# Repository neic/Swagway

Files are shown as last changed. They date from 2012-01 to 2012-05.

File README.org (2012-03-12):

* Swagway
The Swagway is a Segway clone.

It is a school project at HTX Frederikshavn.

** Mechanical
It consists of a welded steel frame with two motors and gearbox assemblies from a powered wheelchair. The motors are 140W each and run on 24V. The batteries are two cheap 12V 18Ah lead batteries.

** Electronics
The electronics is build around an Arduino. It gets it input from a ADXL345 accelerometer and a ITG-3200 gyro and drives the motors through two HEXFET bridges.

The schematic and board layouts are in Electronics/

** Software
The software for the Arduino onboard the Swagway is located in Software/swagway/

A Processing application with a rolling graph for debugging the angles is located in Software/graph/

** Rapport
A rapport (in danish) on the complete build process will be located in Rapport/

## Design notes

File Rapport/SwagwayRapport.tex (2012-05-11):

\documentclass[a4paper,final,11pt,oneside,article,danish,table]{memoir}
\checkandfixthelayout
\XeTeXtracingfonts= 1
\usepackage{babel,microtype,verbatim,threeparttable,amsmath,amssymb,unicode-math,hyperref,siunitx,mhchem,tikz,pgfplots,tikz-timing,pdfpages}
\sisetup{per-mode=symbol}
\microtypesetup{final,verbose=silent}
\usetikzlibrary{mindmap,arrows,positioning,shapes}
%\setmainfont[Ligatures={TeX}]{Arno Pro}
\setmainfont{Linux Libertine O}
\setmathfont{[Asana-Math]}
%\hfuzz=1pt
\usepackage[margin]{fixme}
\fxusetheme{color}

\newcommand{\authorvar}{Carl-Emil~Grøn~Christensen \& Mathias~Dannesbo}
\newcommand{\pretitlevar}{Teknikfag~A~eksamen:}
\newcommand{\titlevar}{Swagway} 
\newcommand{\subtitlevar}{0} 
\newcommand{\datevar}{\today} 
\newcommand{\subjectvar}{Teknikfag~A:~El}
\newcommand{\classvar}{EUC~Nord: HTX~Frederikshavn, f11htx3.B}
\newcommand{\teachervar}{Allan~Gilarska}

\makepagestyle{articlehead}
\makeevenhead{articlehead}{}{\classvar\\\titlevar}{\datevar}
\makeevenfoot{articlehead}{}{\thepage}{}
\makeoddhead{articlehead}{}{\classvar\\\titlevar}{\datevar}
\makeoddfoot{articlehead}{}{\thepage}{}
\pagestyle{articlehead}

\usepackage{listings,textcomp}
\lstset{language=[Visual]C++,
  morekeywords={[2]abs,acos,asin,atan,atan2,ceil,constrain,cos,degrees,exp,floor,log,map,max,min,radians,random,randomSeed,round,sin,sq,sqrt,tan,bitRead,bitWrite,bitSet,bitClear,bit,highByte,lowByte,analogReference,analogRead,analogWrite,attachInterrupt,detachInterrupt,delay,delayMicroseconds,digitalWrite,digitalRead,interrupts,millis,micros,noInterrupts,noTone,pinMode,pulseIn,shiftIn,shiftOut,tone,Serial,Serial1,Serial2,Serial3,begin,end,peek,read,print,println,available,flush,setTimeout,find,findUntil,parseInt,parseFloat,readBytes,readBytesUntil},
  keywordstyle={\bfseries\color[rgb]{0,0,1}},
  keywordstyle={[2]\bfseries\color[rgb]{0.8,0.33,0}},
  identifierstyle=\ttfamily,
  commentstyle=\color[rgb]{0.133,0.545,0.133},
  stringstyle=\color[rgb]{0.627,0.126,0.941},
  showstringspaces=false,
  basicstyle=\small\ttfamily,
  numberstyle=\footnotesize,
  numbers=left,
  stepnumber=1,
  numbersep=10pt,
  tabsize=2,
  breaklines=true,
  breakatwhitespace=false,
  upquote=true,
  extendedchars=true,
  literate={æ}{{\ae}}1
    {ø}{{\o}}1
    {å}{{\aa}}1
}

\tikzstyle{block} = [draw, fill=blue!20, rectangle, 
    minimum height=1.5em, minimum width=5em]
\tikzstyle{sum} = [draw, fill=blue!20, circle, node distance=1cm]
\tikzstyle{input} = [coordinate]
\tikzstyle{output} = [coordinate]

\newcommand{\swino}[2]{\lstinputlisting[firstnumber=#1,firstline=#1,lastline=#2]{../Software/swagway/swagway.ino}}
\newcommand{\adxlh}[2]{\lstinputlisting[firstnumber=#1,firstline=#1,lastline=#2]{../Software/swagway/ADXL345.h}}
\newcommand{\adxlc}[2]{\lstinputlisting[firstnumber=#1,firstline=#1,lastline=#2]{../Software/swagway/ADXL345.cpp}}
\newcommand{\itgh}[2]{\lstinputlisting[firstnumber=#1,firstline=#1,lastline=#2]{../Software/swagway/ITG3200.h}}
\newcommand{\itgc}[2]{\lstinputlisting[firstnumber=#1,firstline=#1,lastline=#2]{../Software/swagway/ITG3200.cpp}}
\newcommand{\boarddate}[1]{\marginpar{\tiny\textcolor{blue!80!black}{#1}}}
\newcommand{\issue}[1]{\textsuperscript{\textcolor{blue!80!black}{\href{https://github.com/neic/Swagway/issues/#1}{\##1}}}}

\begin{document}
% \includepdf{forside.pdf} \clearpage%------------------------ Forside

\noindent
{\fontsize{90}{108}\selectfont \color{red!80!black}\titlevar}\\
\vfill
\noindent
{\color{blue!90!black} \LARGE
{\fontsize{16.55}{20}\selectfont \authorvar}\\
\begin{tabular*}{\textwidth}{@{\extracolsep{\fill}} ll}
  \subjectvar & \datevar\\
\end{tabular*}
}

\thispagestyle{empty}
\clearpage
\includepdf{TroogLove.pdf}
\includepdf{TroogLove.pdf}
\begin{center}
  \if\pretitlevar 0
  \else{\Large\pretitlevar\\} \fi
  \textsc{\HUGE\titlevar\\}
  \if\subtitlevar 0
  \else {\Large\subtitlevar\\} \fi
  %\vspace{1em}
  {\LARGE 
  af\\
   \authorvar}\\
\end{center}

\vfill

\noindent
\begin{tabular*}{\textwidth}{@{\extracolsep{\fill}} ll}
  \classvar&\subjectvar\\
  {Lærer: }\teachervar & \datevar\\
\end{tabular*}
\thispagestyle{empty}
\clearpage

\chapter*{Forord}\label{chap:for}
Gennem teksten vil der være angivet link til “Issues” på GitHub siden for projektet.\footnote{\url{https://github.com/neic/Swagway}} Disse Issues har været brugt som projektstyring samt bugtracker igennem projektforløbet. Links er angivet som i enden af denne sætning.\issue{1} Det er ikke nødvendigt for forståelsen af denne rapport at følge linksne.

Vi vil gerne takke Steffen Linnerup Christiansen for hjælp med mekanikken, samt Kristian Holm Nielsen for hjælp med forståelsen af PID.

\clearpage \setcounter{tocdepth}{1} \tableofcontents \clearpage

\chapter{Indledning}\label{chap:ind}
Transport enheder bliver mere og mere avancerede, og der skabes ofte nye enheder. Specielt mobilitet og anvendelighed har været i højsædet i mange nye produkter. Det handler om hurtigt at kunne komme fra punkt a til punkt b, uden at det kræver større besvær. Derudover er løsninger som er intuitive at bruge også fremskreden, og et produkt som opfylder alle disse punkter er Segwayen. Den er hurtig, kræver næsten ingen erfaring at køre på og er lille. Man kan hurtigt suse fra en afdeling til anden. 

Formålet med projektet er at bygge en motoriseret selvbalancrende tohjulet transportenhed. Det er en klon af en Segway som er et kommercielt produkt. Kendetegnet ved Segwayen er, at de to hjul sidder på samme aksel, hvor elektronik og motorene sørger for at, selv med en fører, holde enheden i balance.
\begin{figure}[htbp]
  \centering
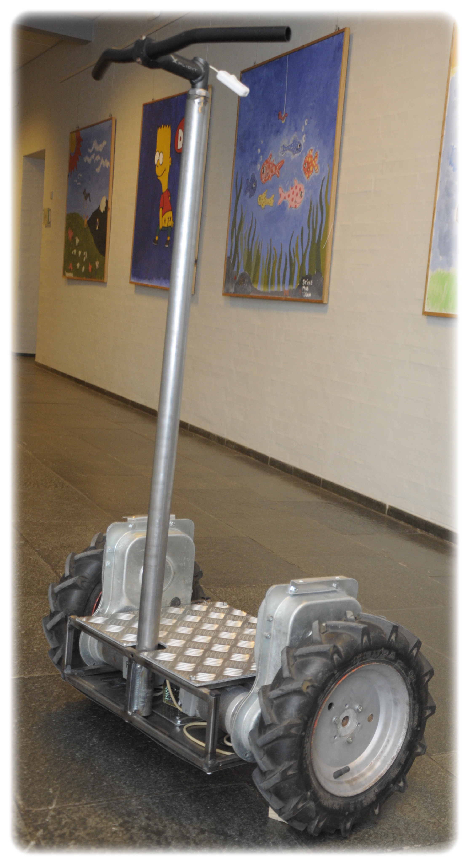
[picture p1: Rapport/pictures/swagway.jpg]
  
  \caption{Den mekaniske udformning af Swagway}
  % \label{fig:}
\end{figure}
Når en fører læner sig frem eller tilbage, kompenserer Segwayen ved køre i samme retning, for atter at balancere den. For at dreje enheden vipper føreren håntaget til den ene eller anden side, som man ønsker at dreje til. Segwayen kan købes for cirka halvfjerdstusinde kroner, hvis man ønsker at eje sådan en.

Projektoplæget lyder:
\begin{quote}
  Formålet er at bygge en balance robot på to hjul,v z en Segway klon. Minimums målet er at få robotten til at balancere. Derefter få den til at køre og kunne styre den hvis tid og evner rækker til det.
\end{quote}

Hovedeudfordringen er at holde enheden lodret. For at gøre dette skal man kende enhedens vinkel i forhold til lodret og omsætte denne vinkel til et signal til motorene. Når vinklen stiger driver motorene hjulene som så flytter enheden og brugerens tygdepunk ind over akslen igen.
Det kan se som tre isolerede problemstillinger som passer ind i I-C-O-modellen:
\begin{itemize}
\item[Input] Måle Swagwayens hældning i forhold til lodret
\item[Control] Omsætte vinklen til et signal til motorene.
\item[Output] Drive to motore baseret på signalet.
\end{itemize}

Projektet er udarbejdet ud fra mikrokontrolleren Arduino Uno, i programmet arduino. Mikrokontrolleren bliver programmeret via. programmet Arduino, som nærmest er i sproget C++ med et Arduino bibliotek. Da vi har modtaget undervisning i denne platform, har dette været det oplagte redskab at benytte til løsningen.

\chapter{Input}
\section{Sensor}
Efter nogen research af andre køretøjer og mindre robotter der fungerer på sammen måde, var det klart at gyroskoper og accelerometere kunne måle vinklen så hurtigt og præcist som det var krævet.
\subsection{Sensor hardware}
Gyroskoper og accelerometere har indtaget forbrugerens produkter, og kortlægger allerede nu deres bevægelser. De faldende priser og faldene energiforbrug har gjort, at gyroskoper og accelerometere er langt mere tilgængelige for alle. Mobiltelefoner, spilkonsoller og kameraer kan nu måle hvordan du bevæger dig, og flere og flere enheder importerer også disse bevægelses sensorer, for at adskille sig fra de andre.

Disse bevægelses sensorer er avancerede MEMS (mikroelektromekaniske systemer) teknologier, som inkoorpererer gyroskoper, accelerometere og kompas sensorer. % Bevægelses behandling foretages oftest med en kombination af to sensorer, for at få optimal præcision.
I dette projekt har vi arbejdet med gyroskoper og accelerometere, som vi også kender fra vores smartphones. Swagwayen skal, lige som en smartphone kan måle om den står eller ligger ned, måle i hvilken vinkel den står i.   

\subsubsection{Gyroskop}
Et gyroskop måler vinkelhastigheder, hvor hurtigt noget drejer om en akse. Hvis denne vinkelhastighed integreres over tid finder man vinklen som gyroskopet har flyttet sig. Problemet med at integrere gyroskopdata er, at pga. måleusikkerheder vil det målte nulpunkt drive væk fra det fysiske nulpunkt. Moderne gyroskoper er en MEMS. Det betyder, at det både er en mekanisk og elektrisk funktion i et system.

\subsubsection{Accelerometer}
Et accelerometer kan måle accelerationer. Man kan med hjælp fra tangens og data fra to akser udregne den vinklen accelerometeret står i forhold til jordens tyngdekraft. Problemet med dette er at accelerometer måler alle accelerationer, ikke kun jordens tyngdekræft. Når Swagwayen fx accelerer, bremser eller køre over en sten bliver den udregnede vinkel forkert, da denne også frembringer en spike i accelerationsmålingen.
\begin{figure}[htbp]
  \centering
  
  \caption{Et accelerometers interne MEMS-struktur}
  \label{fig:memsacc}
\end{figure}
Et accelerometer måler en bevægelse, som enten er forårsaget af tyngdekraften eller en bevægelse. Som set på figur \ref{fig:memsacc} måles accelerationen i et moderne MEMS accelerometer ved en ændring i kapacitansen, $c$, som skyldes en ændring i massen, $m$, position. Kapasitansen fører til en ændring i spændingen, som herefter digitaliseres via ADC og kan benyttes af en mikrokontroller som Arduinoen. Dette gøres for de tre akser x, y og z, og accelerationen kan nu måles i alle retninger.

\subsubsection{IMU}
For at løse problemet med at gyroskopet driver og problemet med at accelerometret ikke er nøjagtig når det bliver påvirket af andre accelerationer end tygdekraften kan man bruge begge sensorer sammen. Man bruger begge sensoreres data og samler dem i et filter. Se mere herom i sektion \ref{sec:filter}.

De fleste moderne accelerometere og gyroskoper kommer i små SMD pakker som er vanskelig håndlodde. Heldigvis er det forholdsvis let at få disse sensorer monteret på et breakoutboard. Efter at have kigget på andre Segway kloner og balancerobotter faldt valget på en IMU fra Sparkfun. Se figur \ref{fig:imu}. En inertial measurement unit, IMU, er en enhed som kombinerer flere sensorer.
\begin{figure}[htbp]
  \centering
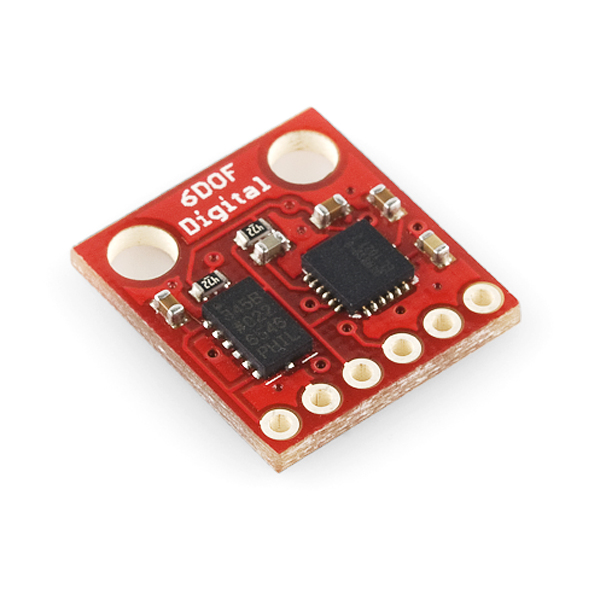
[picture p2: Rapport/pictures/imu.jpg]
  
  \caption[6DOF IMU breakoutboard fra Sparkfun]{6DOF IMU breakoutboard fra Sparkfun. (CC BY-NC-SA 3.0, Sparkfun)}
  \label{fig:imu}
\end{figure}
IMUen fra Sparkfun et ADXL345 accelerometer og et ITG-3200 gyroskop. Accelerometret og gyroskopet er begge tre-akset. Det giver IMUen seks frihedsgrader (DOF). Swagwayen skal dog kun bruge tre frihedsgrader; to akser fra accelerometret og en fra gyroskopet, men IMUen med seks frihedsgrader var det mindste med digital interface.

\subsection{I²C}
Kommunikation med IMUen sker digital over en I²C-bus. På bussen er der en master\footnote{Det er mulig at lave et multi-master opstilling hvis alle masterne understøtter det.} og en eller flere slaves. I Swagwayen er Arduinoen master og accelerometeret og gyroskopet er begge slaves. I²C bussen består af to fysiske forbindelser, en serial data linje (SDA) og en serial clock linje (SCL). Alle enheder på bussen forbinder til disse to forbindelser. Linjerne er open-drain med eksterne pull-op modstande. Det vil sige at i hver enhed sidder der MOSFETer der trækker spændingen på linjen mod GND efter behov. De eksterne pull-op modstande trækker linjerne op igen. Se figur \ref{fig:i2cbasic}.
\begin{figure}[htbp]
  \centering
  
  \caption{Eksempel på I²C-netværk}
  \label{fig:i2cbasic}
\end{figure}

På Arduinoen er I²C SDA på A4 og SCL på pin A5 med indbygget pull-up modstande på \SI{20}{k\ohm}--\SI{50}{k\ohm}. \cite[s. 317]{atmega} De er aktiveret som standard når man bruger Wire biblioteket.\footnote{For reference se linje 75 i \texttt{utility/twi.c} i Wire biblioteket.}

Arduinoens spænding er \SI{5}{V} og IMUens er \SI{3,3}{V}. IMUen bliver forsynet med \SI{3,3}{V} fra Arduinoen, men SDA og SCL er koblet direkte til Arduinoens pins som har \SI{5}{V} som reference. Den korrekte løsning ville være at lave en level-shifter imellem en \SI{5}{V}- og en \SI{3,3}{V}-del af I²C-bussen, men når pull-up modstandene er så høje som de er det stadig forsvarligt at kører IMUen direkte med \SI{5}{V} som $V_{IO}$-reference. Der er flere eksempler på det samme blandt andre på Internettet der bruger samme chips.

Den letteste måde at kommunikere over I²C fra en Arduino er at bruge Wire-bibliotektet som kommer sammen Arduino-softwaren: \lstinline{#include <Wire.h>} For at få Arduinoen til at tilslutte sig bussen som master kaldes \lstinline{Wire.begin();} uden parametre. Slaverne på I²C-bussen har alle en adresse som fremgår af deres respektive datablade.

ADXL345 og ITG-3200 indeholder begge flere register med forskellige funktioner. Nogle registre indeholder opsætningen for chippen, andre indeholder det data som chippen måler. Hvis man, fra Arduinoen, vil skrive til et af registrene køre man følgene kode:
\begin{lstlisting}
  Wire.beginTransmission(deviceAddress);   // begynder en session med enheden med deviceAddress
  Wire.write(regAddress); // sender adressen på den register man vil ændre
  Wire.write(value); // sender værdien registeren skal indtage
  Wire.endTransmission(); // afslutter sessionen
\end{lstlisting}

At læse et register er lidt mere omfattende:
\begin{lstlisting}
 Wire.beginTransmission(deviceAddress); // begynder en session med enheden med deviceAddress
 Wire.write(regAddress); // sender adressen på den register man vil ændre
 Wire.endTransmission(); // afslutter sessionen
  
 Wire.beginTransmission(deviceAddress); // begynder en ny session
 Wire.requestFrom(deviceAdress, numberOfBytes); // sender anmodning på at modtage numberOfBytes
 int i = 0; 
 while (Wire.available()) { // så længe der er data tilgængeligt
   buffer[i] = Wire.read(); // modtag data og fyld det i buffer
   i++;
 }
 Wire.endTransmission(); // afslutter sessionen
\end{lstlisting}

Disse to funktioner bliver senere refereret til som hhv. \lstinline{writemem()} og \lstinline{readmem()}.

\subsection{IMU biblioteker}
I begyndelsen af projektet var alt kommunikationen med ADXL345 og ITG-3200 programmeret i \texttt{swagway.ino}. Det virkede og Arduinoen modtog data fra IMUen, men koden var svær at vedligeholde og gik tit i stykker. Der var desuden en fejl igennem lægere tid der resulterede i at den vinkel der blev udregnet fra gyroskopet, \lstinline{gyroAngle}, var ca. dobbelt så stor som den burde være.\issue{20} Efter mange ufuldendte forsøg på at rette fejlen blev alt gammel kode der var releateret til I²C slettet. Der blev istedet brugt et bibliotek passende til gyroskopet hvor alle funktioner var implementeret. Biblioteket hedder ITG-3200.

Det var ikke til at finde et ligende bibliotek til accelerometret, så med inspiration fra itg3200-bibliotekt blev der skrevet et. Biblioteket består af to filer. En headerfil, \texttt{ADXL345.h}, og selve funktionaliteten, \texttt{ADXL345.cpp}.

Headerfilen indeholder først definitioner på konstanter som enhedsadressen og registere:
\adxlh{23}{35}
Værdierne og navnene er hentet fra \cite[s. 23]{adxl345} At have definitioner på alle konstanter gør koden lettere læselig, så man ikke skal søge referencer i databladet.

Efterfølgene er der defineret en klasse med alle funktioner relateret til accelerometeret:
\adxlh{37}{49}

I \texttt{ADXL345.cpp} er funktionalitet skrevet. Som eksempel er her tre af de første funktioner er begge til opsætning af accelerometret.

\subsubsection{setMeasureMode()}

\adxlc{33}{36}
\lstinline{setMeasureMode()} skriver til power control registret, \lstinline{POWER_CTL}. Funktionaliteten af \lstinline{POWER_CTL} er beskrevet i \cite[s. 25--26]{adxl345}. \lstinline{POWER_CTL}s adresse er, som tidligere beskrevet, defineret i \texttt{ADXL345.h}. \lstinline{MEASUREMODE} er en sekvens af otte bits (en byte) somm hvis de skrives i \lstinline{POWER_CTL}, vil sætte accelerometret i måle tilstand. Sekvensen er ligledes udledt af \cite{adxl345}. Den er i dette tilfælde \texttt{0000\,1000}.

\subsubsection{getOutputRate()}

\adxlc{38}{42}
\lstinline{getOutputRate()} læser registret \lstinline{BW_RATE}, ligger dataene i en buffer og retunerer aflæsningen.

\subsubsection{setFullRes()}

\adxlc{56}{60}
\lstinline{setFullRes()} skal kun ændre \emph{en} bit i registret \lstinline{DATA_FORMAT}. For at bibeholde de andre bits læser den først det som står i registret og gemmer det i en buffer. \lstinline{1 << 3} betyder en bit shiftet tre pladser til venstre: \texttt{0000\,1000}.  \lstinline{~(1 << 3)} er Bitwise NOT værdien af dette: \texttt{1111\,0111}. Det bliver AND med bufferen, \lstinline{(_buff[0] & ~(1 << 3))}. Det er lig med alle de bit som er sat i bufferen på nær den fjerde sidste. Altså: den sætter den fjerde sidste bit til 0 og bibeholder alle andre. \lstinline{(_fullRes << 3)} er værdien der skal sætte shiftet tre pladser til venstre: \texttt{0000\,x000}. Disse to værdier bliver til slut OR med hinanden og den fjerde sidste bit er nu ændret til værdien af \lstinline{_fullRes} uden at nogle andre bits bliver ændret. Denne værdi bliver nu skrevet tilbage i samme buffer.

To andre eksempler på funktionaliteten af \texttt{ADXL345.cpp}. Disse funktioner har med modtagelse af data at gøre.

\subsubsection{isRawDataReady()}
\adxlc{75}{79}
Accelerometeret har et register med interrupt flag, \lstinline{INT_SOURCE}. \lstinline{isRawDataReady()} læser dette register og gemmer det i en buffer. Bufferen bliver shiftet syv pladser til højre og  \lstinline{isRawDataReady()} returnerer en bool værdi, alt efter, om interrupt flaget er sat.

\subsubsection{readAccRaw()}
\adxlc{99}{105}
Dataen i accelerometeret fylder seks registre af 8 bit. Hver akse fylder to registre hvoraf det første er den mindst betydene. \lstinline{readAccRav()} læser \lstinline{DATAX0} og seks registre frem. Dataen bliver lagt i et buffer-array. Den mest betydene af de to bytes som hører sammen bliver shiftet 8 pladser til venstre og derefter AND med den mindst betydene. De to bytes bliver sat sammen direkte efter hindanden. Værdierne bliver retuneret til tre integer-pointers.

\section{Styring}
Styringen af Swagwayen skulle være en længerevarende og holdbar løsning. Det ønskes ikke, at enheden efter forholdsvis kort tid skulle udskiftes eller repareres. Vi overvejede fem forskellige løsninger: En lineær potentiometer, et drejepotentiometer, gaffelsensor, strain-gate og stepper motor.
\subsection{Lineær potentiometer} 
Et lieært potentiometer fungerer som et normalt potentiometer, dog trækkes "armen" i en sliske.
Potentiometret skal placeres i bunden af stangen, hvorefter potentiometrets arm trækkes med stangens bevægelse. Herefter vil man kunne ændre på PWM signalet til motorene, og på den måde dreje. Løsningen er simpel at udføre, og vil virke let i praksis.

Ulempen ved denne løsning er dog, at potentiometret hurtigt slides op ved brug, og det er derfor ikke en holdbar løsning.
\subsection{Dreje potentiometer}
Samme princip fra det lineæere potentiometer gælder her. Derimod drejes dette potentiometer i stedet for om sin egen akse. Ideen med dette var, at man let kan implementere den i toppen af Swagwayens styr, og så styre PWM signalet til motorerene sådan. 

Lige som det linæere potentiometer, slides denne løsning hurtigt, og er derfor ikke holdbar. Derudover er denne løsning ikke lige så intuitiv og føles klodset, hvilket ikke er det vi ønsker med produktet.
\subsection{Gaffelsensor}
Gaffelsensorer benyttes i gamle kuglemuse, som vi alle nok kender. Gaffelsensorene måler hvor meget noget har flyttet sig ved at analysere bevægelsen i forhold til nogle bånd buede bånd, i to krysende retninger. Ud fra bevægelsen kan gaffelsensoren bestemme, hvordan kuglen har bevæget sig i dens socket. En lignende anordning kunne placeres i bunden af stangen lige som det lineæere potentiometer, og en kugle kunne skubbes rundt lige som i en mus, for at bestemme stangens hældningen. Løsningen er meget præcis hvis den er lavet mekanisk godt.

Gaffelsensoren er derimod ekstremt upræcis hvis mekanikken ikke er rentskåret-næsten perfekt. Yderligere bliver dens præcision påvirket af støv og skidt, hvilket hurtigt vil ophobe sig i bunden af vores Swagway.
\subsection{Strain-gate}
En strain-gate løsning er en anordning, som placeres på siden af stangen. Strain-gaten kan mærke tryk i metallet, og kan ud fra dette tryk bestemme en værdi, som man kan bruge til at styre Swagwayen med. Denne løsning er ekstrem præcis, og benyttes ofte i store maskiner.

Problemet er dog, at den ikke virker på vores stang, da den er for stiv, og løsningen hverken er intuitiv eller responsiv for forbrugeren. Den er ikke lige til at finde ud af fra første øjekast, og den er sværere at lære.
\subsection{Stepper motor}
Det sidste løsningsforslag: Stepper motor. Planen med denne var at foretage den modsatte funktion af hvad man normalt gør med en stepper motor: I stedet for at få motoren til at bevæge noget, skal styret bevæge motoren, hvorefter det måles hvilket step den er på i Arduinoen. Løsningen er ekstremt robust og præcis, som vi kender stepper motorer for. Derudover vil den ikke være modtagelig for omgivelsernes påvirkninger i form af støv eller andet snavs. Yderligere kan steppene geares, så den bliver endnu mere præcis hvis nødve
+ndigt.

Det sværeste ved denne løsning er, at implementere den. 

Hvis tiden havde rækket til det, havde vi derfor valgt denne som den umiddelbare løsning, da den ikke påvirkes af udefrakomne krafter, og det eneste umiddelbare problem er implementeringen.
\chapter{Control}
\section{Hoved loop}
Hoved loopet i \texttt{swagway.ino} er forholds kort fordi de fleste funktioner er flyttet til biblioteker eller metoder. Hele loopet består af tre \lstinline{if()}-statements. I det første bliver accelerometeret spurgt om der er nye data klar. Hvis det er tilfældet bliver dataende hentet og \lstinline{atac2()} bliver brugt til at udregne vinklen ud fra $xy$-planet. Et flag der indekerer at der er ankommet nye data fra accelerometeret sættes til \lstinline{true}.

Derefter bliver gyroskopet spurgt om der er nye data klar. Hvis de er det bliver de ligeledes hentet. Data fra gyroskopets $z$-akse integrers.\footnote{Integralet af gyroskobets $z$-akse bruges ikke direkte til at balancere. Det sendes kun over serielporten til debugging og tuning af Kalman-filteret.} Et tilsvarende flag der indekerer at der er ankommet nye data fra gyroskopet bliver stat til \lstinline{true}.
\swino{102}{130}
Når flagende indikerer at der er nye data fra både accelerometeret og gyroskopet sendes dataende til Kalman-filtert som retunerer en estimeret vinkel. (Se afsnit \ref{sec:filter} for forklaring hvordan det virker.) Vinklen sendes videre til regulering (se afsnit \ref{sec:regulering}) som retunerer en PWM-værdi som sendes til motoren. 
\section{Filter}\label{sec:filter}
Målet med filtret er at samle dataen fra gyroskopet, accelerometeret og ud fra disse beregne en vinkel, som vi kan benytte til at regulere PWM efter. Ud fra dette mål, udvalgte vi tre filtre, som har de egenskaber vi leder efter.
\subsection{Komplementær filter}
Det komplementære filter er kendetegnet ved, at det er let at sætte op, fordi det er meget intuitivt. Filtret hjælper også kraftigt på støj og drifting. Derudover er det hurtigt, hvilket betyder at Arduinoen kan beregne vinklen i nærmest real-time. 

Filtret består af et lav pas filter på accelerometeret, som kun lader længerevarende ændringer igennem, hvilket fjerner de problemer accelerometeret har med bevægelses-acceleration. Gyroskopets data passerer igennem et høj pas filter, som fjerner længerevarende ændringer. De længerevarende ændringer som gyroen er udsat for er drifting. Når de to svagheder er reduceret kraftigt vha. det komplementære filter, ender man med en vinkel der ligger meget nær virkeligheden.
\subsection{Kalman filter}
Kalman filtret er et professionelt filter, som benyttes i de fleste køretøjer nutildags, da dette filter er yderst præcis. Kalman filtret er desværre også ekstremt svært at forstå, men fungerer i princippet lige som det komplementære: Det fjerne støj fra de to enheder, og reducerer kraftigt deres ulighed. Kalman filtret er klart det bedste da den selv korrigerer dens gain med tiden - den lærer jo længere tid den kører. Desværre kræver Kalman filtret en ekstraoordinær viden inden for matematik.

\section{Regulering}\label{sec:regulering}
For at kontrolere hvorledes Swagwayens motorer bevæger sig i forhold til vinklen, skal vi bestemme et forhold mellem vinklens hældning og PWM. 
\subsection{Lineær}
Den simpleste og mest basale reguleringsteknik til at holde Swagwayen i balance er et lineært filter. Her mappes PWM mellem et og treddive, hvorefter den forøges med en, hver gang vinklen stiger med en i den ene eller anden retning. Swagwayen vil derfor stige lineært i hastighed med den vinkel som den hælder med.

Den lineære regulering fungerer fint uden en fører eller med andet formål end blot at balancere.
\subsection{PID}
Proportional-Integral-Differential kontroller er en loop feedback mekanisme. PID kontrollerer en stor del af industrielle kontrolsystemer, da det er en feedback controller: Den beregne en "fejl" som er forskellen mellem den ønskede handling og den udførte. PID kontrolleren forsøger herefter at minimere fejlen ved at justere på kontrol input. PID forsøger derfor at opretholde eks. vinklen konstant ved det ønskede, ved hele tiden at justere sig selv. 

PID er delt op i tre dele: 
Et proportionalt gain $K_P$, som ganges med fejlen i systemet.
Integralet af fejlen over tid, som ganges med $K_I$, for at fjerne fejlen omkring nul punktet, også kaldet steady-state.
Differentialet af hvor hurtig fejlen ændrer sig, ganges med $K_D$. Hvis der sker en hurtig ændring, bliver $K_D$ meget stor for at kompensere.

Disse tre dele gør op for PID, som sørger for, at fejlen justeres lige meget hvilken måde den ændres.

Vi startede med at implementere PID til at regulere den, men erfarede hurtigt at det ikke virkede. For at PID virker, er det vigtigt at den fejl man beregner, stammer fra kilden. Efter som vi ikke havde encodere på motorene kunne vi ikke bestemme hvordan motorene reagerede. Så i stedet for at beregne forskellen mellem den ønskede handling og den udførte, beregnede vi forskellen mellem den ønskede handling og den handling PWM signalet sendte. Se figur \ref{fig:pid} for en grafisk forklaring. For at PID kontrollen skal fungere, skal der foretages målinger efter motoren, vist med den blå linje, hvorimod vi foretog målingerne før motoren, vist med den røde linje.
Da tiden var ved at løbe ud, bestemte vi os for at lade PID og encoderne ligge, og gå videre til en ny løsning.

\begin{figure}[htbp]
  \centering
  \begin{tikzpicture}[auto, node distance=2cm,>=latex']
    \node [block, minimum width=7em] (gyro){Gyroskop};
    \node [block, below of=gyro, node distance=1cm,minimum width=7em] (acc) {Accelerometer};
    \node [block, right of=gyro, node distance=3cm] (kal) {Kalman};
    \node [sum, right of=kal, node distance=1.5cm] (sum1) {};
    \node [block, right of=sum1, node distance=2cm] (i) {$I$};
    \node [block, above of=i, node distance=1cm] (p) {$P$};
    \node [block, below of=i, node distance=1cm] (d) {$D$};
    \node [sum, right of=i, node distance=1.5cm] (sum2) {};
    \node [block, right of=sum2, node distance=2cm] (motor) {Motor};

    \draw [->] (gyro) -- (kal);
    \draw [->] (acc) -| (kal);
    \draw [->] (kal) -- (sum1);
    \node [right of=sum1, node distance=0.5cm] (sum11){};
    \draw [->] (sum11) |- (p);
    \draw [->] (sum1) -- (i);
    \draw [->] (sum11) |- (d);

    \draw [->] (p) -| (sum2);
    \draw [->] (i) -- (sum2);
    \draw [->] (d) -| (sum2);

    \draw [->] (sum2) -- (motor);

    \node [right of=motor, node distance=1.5cm] (end) {};
    \draw [dashed, thick, blue] (motor) -- (end);
    \node [below of=sum1, node distance=2cm] (sum12) {};
    \draw [dashed, thick, blue] (end) |- (sum12);
    \draw [dashed, thick, blue, ->] (sum12) -- (sum1);

    \node [above of=sum1, node distance=2cm] (sum13) {};
    \node [right of=sum2, node distance=0.5cm] (sum21){};
    \draw [dashed, thick, red] (sum21) |- (sum13);
    \draw [dashed, thick, red, ->] (sum13) -- (sum1);
  \end{tikzpicture}
  \caption{Motor regulering}
  \label{fig:pid}
\end{figure}
\subsection{Eksponentiel}
I stedet for PID introducerede vi en eksponentiel funktion. Den eksponentielle funktion får PWM signalet til at stige som en normal eksponentiel funktion stiger. Variablerne som funktionen er opstillet efter er fundet ud fra trial and error princippet. Nedenfor ses implementationen af reguleringen:
\swino{54}{58}

\swino{168}{180}

Den eksponentielle funktion er den som sidder i det nuværende produkt. Vi kan med denne funktion køre på Swagwayen uden at falde, og den kan holde sin position uden at stå og "rykke" hårdt fra side til side.
\chapter{Output}
For at holde Swagwayen i balance, ønsker vi, ligesom Segwayen, at motorene skal kunne køre i begge retninger med en variabel hastighed.
\section{H-broens virkemåde}
\label{sec:H-broen}
H-broen bruges til kontrol af motore. Se figur \ref{fig:hbro}
En H-bro er fire kontakter sat op som et H, med en motor i midten. A og B kontakterne på en side må ikke være trykkede nede samtidigt, så kører strømmen uden om motoren. Derudover må man ikke tænde for C og D for så kortslutter den. Hvis man derimod tænder for enten A og D, eller C og B, bevæger motoren sig i den retning strømmen løber. Man tænder altså derfor H-broen i par af to modsatte: A og D samtidigt, og C og B samtidigt.
\begin{figure}[htbp]
  \centering
  
  \caption{Diagram over simpel H-bro}
  \label{fig:hbro}
\end{figure}

H-broen på Swagwayen er lidt mere kompleks. Hele logikken kan findes på tabel \ref{tab:sandhed}. 
\section{PWM}
Pulsbreddemodulation (Pulse-Width-Modulationer en metode til at kontrollere mængden af strøm i elektriske apparater. 

PWM leverer strøm ved at sende en impuls, med variabel tid mellem 0 og 255. Jo mere tallet nærmer sig 255, jo længere tid er det elektriske apparat som er tilsluttet tændt. Se figur \ref{fig:pwm}

Måden vi styre dette på i en Arduino er via \lstinline{analogWrite(pin,\dots);}. Her har vi mulighed for at give en værdi fra 0--255. Dette betyder at \lstinline{analogWrite(pin,255);} er 100\% og \lstinline{analogWrite(pin,127);} er 50\%.
\begin{figure}[htbp]
  \centering
  
  \caption{Eksempel på PWM med varierende dutycycle}
  \label{fig:pwm}
\end{figure}

\section{Overvejelser}
Der er to muligheder under fremstilling af en H-bro. Enten kan der benyttes en simpel H-bro chip, eller man kan fremstille en selv. 
Chippen er den nemme løsning, som gør alting super let at arbejde med. Dog kan chippen ikke håndtere store strømme, og det var derfor urealistisk at piggy-back dem.

Vi fremstillede derfor selv en H-bro, da den kan klare de store mængder af strøm vi arbejder med, selvom at det er langt mere komplekst og det forøger kraftigt mængden af ting der kan gå galt.

Efter som at motorene skal kunne køres med variable hastigheder, skal der køres PWM på disse. Man kan vælge, om dette skal ske i toppen eller bunden af H-broen som diskuteret før \ref{sec:H-broen}. Vi startede med at gøre dette i toppen, men dette blev senere ændret til bunden, hvilket er dybere beskrevet i motorcontroller v2.1. \ref{sec:Motorcontroller2.1}
\section{Motorcontroller}

\begin{table}[htbp]
  \caption{Motorcontroller v5.2 sandhedstabel}
  \centering
  % \begin{threeparttable}
  \begin{tabular}{ccc|cccc|ccccl}
    \toprule
    \multicolumn{3}{c}{Arduino pin}&\multicolumn{4}{c}{HEXFET spænding}&\multicolumn{4}{c}{HEXFET on/off}\\
    P7&P6&P5 &Q1&Q2&Q3&Q4 &Q1&Q2&Q3&Q4\\
    P8&P9&P10 &Q5&Q6&Q7&Q8 &Q5&Q6&Q7&Q8\\
    \midrule
    0&0&0 &0&1&0&0 &0&0&0&1 & Off ($\circlearrowright$)\\
    1&0&0 &0&0&0&1 &0&1&0&0 & Off ($\circlearrowleft$)\\
    0&1&0 &1&1&0&0 &1&0&0&1 & $\circlearrowright$\\
    1&1&0 &1&0&0&1 &1&1&0&0 & Short\\
    0&0&1 &0&1&1&0 &0&0&1&1 & Short\\
    1&0&1 &0&0&1&1 &0&1&1&0 & $\circlearrowleft$\\
    0&1&1 &1&1&1&0 &1&0&1&1 & Short\\
    1&1&1 &1&0&1&1 &1&1&1&0 & Short\\
    \bottomrule
  \end{tabular}
  % \begin{tablenotes}
  % \end{tablenotes}
  % \end{threeparttable}
  \legend{Tabellen viser hvordan den seneste motorcontroller, v5.2, opføre sig hvis den får inputtet angivet under “Arduino Pin”}
  \label{tab:sandhed}
\end{table}

H-bro, PWM, PWM-kondensator, beskyttelses dioder, 4000 serie, optocopler

\subsection{Samlet board}
Det var upraktisk at have alle funktioner på samme board. H-broerne og optocouplerne blev flyttet på sit eget board “Motorcontroller v1.0”.

\subsection{Motorcontroller v1.0}
\boarddate{24. januar 2012}
Se figur \ref{fig:oldmotor} øverst til venstre.
\subsubsection{Det var der galt}
Boardet virkede ikke. Det opførte sig som om det var kortsluttet. Det viste sig, at efter boardet var skilt helt af igen, at det plus tegn der skulle vise polariteten, var sat ved den forkerte pol. Printet havde taget skade af at blive loddet på flere gange.

Der var desuden nogle af ledningene for tætsiddene og loddeøerne var lidt underdimensionerede. Der manglede også en mulighed for at se, hvilken vej strømmen løber i H-broerne.
\subsubsection{Det blev der rettet}
Plus tegnet blev flyttet over til den rigtige pol. Ledningerne blev flyttet længere væk fra hinanden, og loddeøernes størrelser forøget.

\subsection{Motorcontroller v2.0}
\boarddate{8. marts 2012} 
\subsubsection{Det var der galt}
Dette board blev aldrig lavet færdigt; Ledningerne omkring pinheaderen var for tæt efter at loddeøeren blev forstørret.

\subsubsection{Det blev der rettet}
Loddeøerne blev gjort en smule mindre for at tillade ledningerners forbipasserend.

\subsection{Motorcontroller v2.1}\label{sec:Motorcontroller2.1}
\boarddate{8 marts 2012}
Se figur \ref{fig:oldmotor} øverst i midten og figur \ref{fig:mosch2.1}.
\begin{figure}[htbp]
  \centering
  
  \caption{Diagram over Motorcontroller v2.1}
  \label{fig:mosch2.1}
\end{figure}
\subsubsection{Det var der galt}

Boardet fungerede umiddelbart. Motoren kunne køre i begge retninger og farten kunne styres med PWM. Dog startede motoren på ca. 30\% fart uintentionelt i den ene retning. Ved at måle på PWM signalet fra mainboardet og signalet til motoren via. et oscilloskop, kunne problemet indskrænkes til at være på Motorcontrolleren.

Det viste sig efter megen debugging, at spændingen på gaten på P-kanal HEXFETerne (IRF4905) ikke gik \lstinline{HIGH} lige så hurtigt som ventet. Der blev opstillet et forsøg på et breadboard med en P-kanal HEXFET, en optocoupler og en Arduino, for at gennemskue problemet.

Forsøget viste, at når optocoupleren sad mellem HEXFETen og Arduinoen var der en ubekendt kapacitet mellem HEXFETens gate og source. Figur \ref{fig:stigetid} viser nederst PWM signalet fra Arduinoen og øverst signalet på P-kanal HTXFETens gate, hvor man tydeligt kan se, at det tager en ubelejlig tid før signalet på gaten stiger.
\begin{figure}[htbp]
  \centering
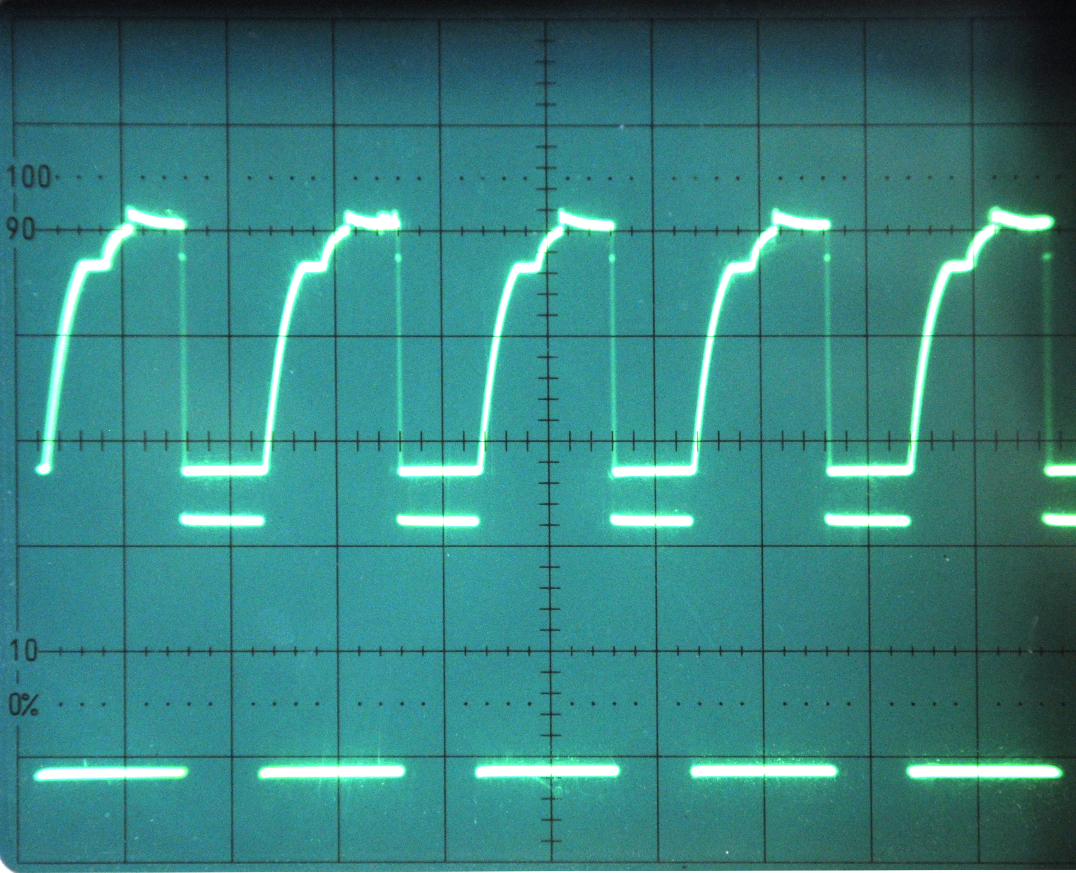
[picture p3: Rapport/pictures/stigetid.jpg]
  
  \caption[Oscilloskop billede af stigetid på en P-kanal HEXFET gate]{Oscilloskop billede af stigetid på en P-kanal HEXFET gate. Nederst ses PWM-signalet fra Arduinoen, øverst ses signalet på HEXFETens gate.}
  \label{fig:stigetid}
\end{figure}

Ved at sætte en mindre pull-up modstand på, kunne gaten aflades hurtigere, men det var ikke muligt at få den tilpas langt ned til at kunne styre motoren godt. Ved at fjerne optocoupleren og køre HEXFETens gate direkte fra Arduinoen eller ved fjerne HEXFETen og måle direkte på optocoupleren, var stigningstiden $\approx0$. Det var kun i kombination mellem HEXFETen og transistoren i optocoupleren, at stigningstiden ikke var $\approx0$.

Der blev forsøgt med en 4N25 optocoupler istedet for 4N35, og en BC547 istedet for optocoupleren; der var samme stigningstid.

Det har ikke været muligt, selv med hjælp fra vejleder, at forklare hvorfor denne kapacitet er der.

Problemet blev ikke løst, det blev bare gjort ubetydeligt: Istedet for at bruge en N- og en P-kanal HEXFET til at bestemme retning og køre PWM på de andre to N- og P-kanal HEXFETer, blev det lavet om til at begge P-kanal HEXFETer blev brugt til at bestemme retning og at N-kanal HEXFETerne bliver brugt at køre PWM. Det er ikke et problem at stigetiden på P-kanal HEXFETerne er langsom da de kun ændre sig når der skiftes retning og ikke med høj frekvens som ved PWM.

For ikke at tilføje flere optocouplere og bruge flere pins på Arduinoen blev der, på motorcontrolleren tilføjet to invertere.
\subsubsection{Det blev der rettet}
Vi byttede om på to P- og N-kanal HEXFETer, så der nu køres PWM på N-kanalen, og P-kanalen bestemmer retning. Derudover blev det tilføjet to invertere på motorcontrolleren.

\subsection{Motorcontroller v3.0}
\boarddate{27. marts 2012}
Se figur \ref{fig:oldmotor} øverst til højre.
\subsubsection{Det var der galt} 
Efter at der blev tilføjet en inverter på to af gatesne til P-kanal HEXFETerne er denne \lstinline{LOW} når der ikke er spænding på optocouplerne (for eksempel når den ikke er koblet til mainboardet). Det tænder HEXFETen sammen med N-kanal HEXFETerne, som også er tændt uden spænding på optocouplerne, hvilket kortslutter H-broen. Motorcontroller v3.0 var fungerede, men det var upraktisk, at den var kortsluttet uden at være koblet sammen med mainboardet.

\subsubsection{Det blev der rettet}
Pull-up modstandende blev derfor erstattet med pull-down modstande.

\subsection{Motorcontroller v4.0}
\boarddate{12. april 2012} 
\subsubsection{Det var der galt} 
Dette board blev aldrig lavet færdigt. 
En stor del af boardet blev re-routed da der var blevet rodet efter mange versioner.
\subsubsection{Det blev der rettet}
Boardet blev rerouted pga. rod.

\subsection{Motorcontroller v4.1}
\boarddate{13. april 2012}
Se figur \ref{fig:oldmotor} Nederst til venstre.
\subsubsection{Det var der galt} 
Der var en ledning der ikke var routed og der var noget mindre re-routing.
\subsubsection{Det blev der rettet}
Rettet op på fejl i routing

\subsection{Motorcontroller v4.2}
\boarddate{17. april 2012} 
\subsubsection{Det var der galt} 
Dette board blev aldrig lavet færdigt.
For-modstandene til optocouplerene sad på mainboardet af en ukendt årsag. Det virkede mere logisk og praktisk at have disse på motorboardet.
\subsubsection{Det blev der rettet}
For-modstandene til optocouplerne blev flyttet fra mainboardet til motorcontrolleren.

\subsection{Motorcontroller v5.0}
\boarddate{24. april 2012} 
\subsubsection{Det var der galt} 
Dette board blev aldrig lavet færdigt.
Det er svært at debugge motorcontrolleren når man ikke kan se hvad der sker. Optocouplerenes manglende tegn på hvad der sker skabte problemer.
\subsubsection{Det blev der rettet}
Der blev tilføjet LEDer til optocouplerne.

\subsection{Motorcontroller v5.1}
\boarddate{24. april 2012} 
\subsubsection{Det var der galt} 
Dette board blev aldrig lavet færdigt.
Logikken blev ændret pga. en fejl.
\subsubsection{Det blev der rettet}
Nogle ledninger i fladkablet blev byttet om.

\subsection{Motorcontroller v5.2}
\boarddate{24. april 2012}
Se figur \ref{fig:oldmotor} nederst i midten.
\begin{figure}[htbp]
  \centering
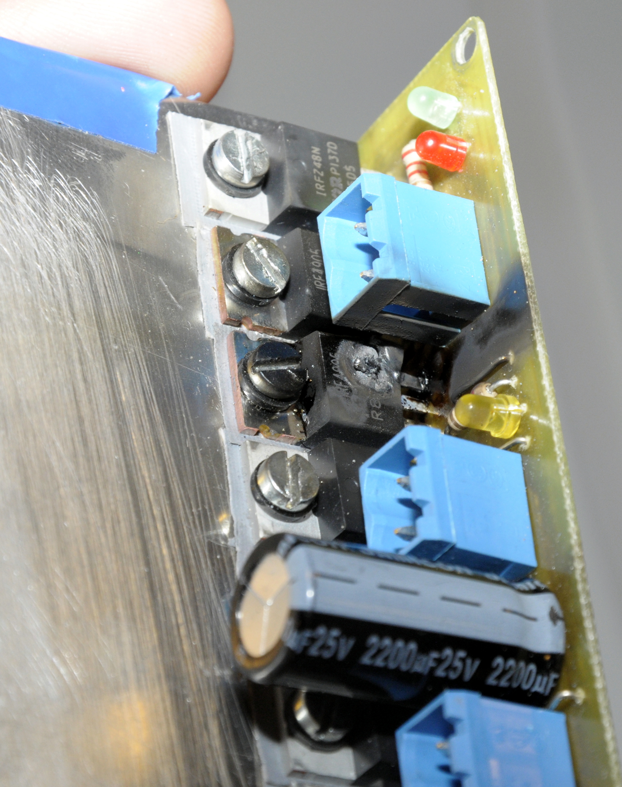
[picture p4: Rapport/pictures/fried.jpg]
  
  \caption{En HEXFET på Motorcontroller v5.2 der er brændt af}
  \label{fig:fried}
\end{figure}
\begin{figure}[htbp]
  \centering
  
  \caption{Diagram over Motorcontroller v5.2}
  \label{fig:mosch5.2}
\end{figure}
\subsubsection{Det var der galt} 
Boardet v5.2 sidder i Swagwayen og fungerer. Den nuværende version er en erstatning af et magen til, da dette brændte af under en længerevarende, ellers succesfuld, prøvekørsel. Se figur \ref{fig:fried}.

Motorene danner strøm når de går i frigang, og hvis man derfor kører hurtigt fremad, og ændrer vinklen til et modsatgående fortegn, sendes strømmen tilbage igennem boardet. Der blev derfor tilføjet beskyttelses dioder for at tage strømmen.
\subsubsection{Det blev der rettet}
Der blev til v6.0 tilføjet beskyttelses dioder til kredsløbet, for at tage strømmen fra motorene.
\subsection{Motorcontroller v6.0}
\boarddate{24. april 2012}
Se figur \ref{fig:oldmotor} nederst til højre.
\begin{figure}[htbp]
  \centering
  
  \caption[Tidligere versioner af Motorcontrolleren]{Tidligere versioner af Motorcontrolleren. Øverste række fra venstre: v1.0, v2.1, v3.0. Nederst række fra venstre: v4.1, v5.2, v6.0}
  \label{fig:oldmotor}
\end{figure}
\chapter{Auxiliary}
\begin{table}[htbp]
  \caption{Pin forbindelser på Arduino}
  \centering
  \begin{threeparttable}
    \begin{tabular}{rll}
      \toprule
      Pin & Forbindelse & Egenskaber\\
      \midrule
      0 & USB Rx & \\
      1 & USB Tx & \\
      2 & Radio Rx & Interrupt\\
      3 & & Interrupt, PWM\\
      4 & Radio Tx & \\
      5 & Motorcontroller R2 & PWM\tnote{a}\\
      6 & Motorcontroller L2 & PWM\tnote{a}\\
      7 & Motorcontroller L1 & \\
      8 & Motorcontroller R1 & \\
      9 & Motorcontroller L3 & PWM\\
      10 & Motorcontroller R3 & PWM\\
      11 & & PWM\\
      12 & & \\
      13 & & LED\\
      A0 & & \\
      A1 & & \\
      A2 & Steering & \\
      A3 & Steering & \\
      A4 & IMU I²C SDA & SDA\\
      A5 & IMU I²C SCL & SCL
    \end{tabular}
    \begin{tablenotes}
      \item[a]{PWM outputtet fra disse er lidt højere end forventet. De drives af en anden timer.\issue{42} Se under Mainboard 4.0 i sektion \ref{sec:main40}.}
    \end{tablenotes}
  \end{threeparttable}
  % \label{tab:}
\end{table}

\section{Mainboard}

\subsection{Mainboard v1.0}
\boarddate{24 jan 2012}
\subsubsection{Det var der galt}
Mainboardets loddeøer var underdimensioneret\issue{1}, hvilket betyder, at lodninger blev besværlige. Yderligere var det ikke til at komme til at trykke på resetknappen på Arduinoen, da shieldet dækkede over knappen.\issue{2} 
\subsubsection{Det blev der rettet}
Der blev tilføjet en reset knap på mainboardet, i den følgende version. Der blev også tilføjet et stik til datamodtagning fra styringen på mainboardet.\issue{12}
Derudover blev loddeøerne udvidet.

\subsection{Mainboard v2.0}
\boarddate{1 marts 2012}
\subsubsection{Det var der galt}
Logik kredsløbet blev kasseret. Efterfølgende blev der brugt tre Arduino pins per motor.\issue{21} Display-boardet blev ligeledes kasseret.\issue{9} Pinheaderne til 9V og IMUen var desuden for tæt sammen.\issue{13}
\subsubsection{Det blev der rettet}
Pinheaderen til 9V batteriet og IMUen blev flttet længere væk fra hinanden. Derudover blev der implementeret nyt logik.

\subsection{Mainboard v3.0}
\boarddate{26 marts 2012} 
\subsubsection{Det var der galt}
Dette board blev aldrig lavet færdig.
På boardet blev der dog tilføjet pins til en radio, hvis formål er at kunne ændre reguleringsværdierne trådløst.\issue{29}
\subsubsection{Det blev der rettet}
-

\subsection{Mainboard v3.1}
\boarddate{29 marts 2012}
\subsubsection{Det var der galt}
For-modstandene var placeret på mainboardet, hvilket var ulogisk.\issue{37}
Pinheader til IMU passer med en 5×2 socket, men der er placeret en 7×2 på boardet.
\subsubsection{Det blev der rettet}
For-modstandene blev flyttet fra mainboardet til motorcontrolleren. Pinheaderen til IMUen blev lavet om til en 5×2 socket.

\subsection{Mainboard v4.0}\label{sec:main40}
\boarddate{24 april 2012}
\subsubsection{Det var der galt}
Swagwayen kører med dette board, men den ene motor kørte hurtigere end den anden.\issue{42} Det lignede umiddelbart en mekanisk fejl, men ved at bytte om på ledningerne til motorene viste det sig at den ene kanal på motorcontrolleren kørte langsommere end den anden. 
Problemet blev isoleret til, at Arduinoen ikke sendte PWM med samme frekvens til begge kanaler. I Arduino referencen for \lstinline{AnalogWrite()} ser man også, at pin 5 og 6 PWM kører fra en anden timer end de andre PWM pins. Tilfældigvis kørte den ene motor på begge af disse pins. 

\subsubsection{Det blev der rettet}
Pin 5 og 9 blev byttet så Swagwayen kører lidt hurtigere forlæns end baglæns, men med samme forskel på begge hjul.

Ombytningen af de to pins blev gjort ved at bryde kobberbanerne på printet og lodde to ledninger på, der blev ikke lavet et nyt board.

\chapter{Mekanik}
Mekanikken i Swagwayen består af to 24V DC motorer som hver kan trække 8A. Motorene blev anskaffet fra en gammel kørestol, som havde en top fart af cirka \SI{13}{km\per h}. Motorene drives af to \SI{18}{\ampere h½} batterier.

\chapter{Konklusion} \label{chap:kon}
Vores mål var at lave en balance robot, hvor vi havde tilvalgt at lave styring til begge sider, hvis tiden rækkede til det.

Swagwayen fungerer som den står idag, og kan balancere på egen hånd. Det viste sig, at lave styring så den kunne dreje var i overkanten af hvad vi kunne nå inden for den givne tidsramme, hvori vi dog opfyldte vores minimumskrav. Swagwayen kan også køre frem og tilbage med en fører.

\chapter{Perspektivering} \label{chap:per}
Som nævnt i projektbeskrivelsen, ville vi gerne med mere tid, have haft implementeret styring i form af stepper motorer til Swagwayen. Derudover ville det være interessant at have haft kraftigere motorer med planetgear for at kunne køre hurtigere og holde Swagwayen mere stabil. De store gear i de nuværende motorer gør den for tung, og inertimomentet for stort.
Hvis vi fortsætter med projektet på et tidspunkt, skal der også tilføjes encodere til motorene for at kunne genimplementere PID for bedre regulering.  

\clearpage
\listoftables
\listoffigures
\nocite{*}
\bibliographystyle{dk-apali} \bibliography{bib}
\clearpage \appendix

\chapter{Arbejdsdeling}
\begin{itemize}
\item[Indledning] Fælles
\item[Sensor teori] Carl-Emil
\item[Sensor: IMU] Mathias
\item[Sensor: I²C] Mathias
\item[Sensor: I²C biblioteker] Mathias
\item[Styring] Carl-Emil
\item[Hoved loop] Mathias
\item[Filter] Carl-Emil
\item[Regulering] Carl-Emil
\item[Output] Carl-Emil
\item[Motorcontrolere] Fælles
\item[Auxiliary] Fælles
\item[Mekanik] Carl-Emil
\item[Konklusion] Fælles
\item[Perspektivering] Fælles
\end{itemize}

\chapter{Kildekode}

\section{\texttt{swagway.ino}}
\lstinputlisting{../Software/swagway/swagway.ino}
\section{\texttt{ADXL345.h}}
\lstinputlisting{../Software/swagway/ADXL345.h}
\section{\texttt{ADXL345.cpp}}
\lstinputlisting{../Software/swagway/ADXL345.cpp}
\end{document}

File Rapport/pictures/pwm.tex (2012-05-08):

\documentclass[oneside,danish]{article}
\usepackage[utf8]{inputenc}
\usepackage[papersize={389pt,215pt},top=0pt, bottom=0pt, left=0pt, right=0pt]{geometry}
\usepackage{amsmath,pgfplots,tikz-timing}

\begin{document}
\begin{tikztimingtable}[timing/coldist=0,xscale=4.5,yscale=3]
    & 8{L}\\
    & G.25H7{.75C.25C}.75C\\
    & Gh7{cc}c\\
    & G.75H7{.25C.75C}.25C\\
    & 8{hh}\\
\extracode
\node[anchor=east,align=right] at (0,.5){\texttt{analogWrite(pin,0);}\\0\%};
\node[anchor=east,align=right] at (0,-1.5){\texttt{analogWrite(pin,63);}\\25\%};
\node[anchor=east,align=right] at (0,-3.5){\texttt{analogWrite(pin,127);}\\50\%};
\node[anchor=east,align=right] at (0,-5.5){\texttt{analogWrite(pin,191);}\\75\%};
\node[anchor=east,align=right] at (0,-7.5){\texttt{analogWrite(pin,255);}\\100\%};
\begin{background}[help lines]
\vertlines{}
\end{background}
  \end{tikztimingtable}
\end{document}

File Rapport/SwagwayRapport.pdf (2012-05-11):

# Swagway

## Carl-Emil Grøn Christensen & Mathias Dannesbo

Teknikfag A: El | 11. maj 2012

Teknikfag A eksamen:
S
af

## Carl-Emil Grøn Christensen & Mathias Dannesbo

Resumé

FiXme: Skriv
resume
EUC Nord: HTX Frederikshavn, f11htx3.B | Teknikfag A: El
Lærer: Alan Gilarska | 11. maj 2012

Swagway

Forord

Gennem teksten vil der være angivet link til “Issues” på GitHub siden for projektet.¹ Disse Issues har været brugt som projektstyring samt bugtracker igennem projektforløbet. Links er angivet som i enden af denne sætning.#1 (https://github.com/neic/Swagway/issues/1) Det er ikke nødvendigt for forståelsen af denne rapport at følge linksne.
Vi vil gerne takke Steffen Linnerup Christiansen for hjælp med mekanikken, samt Kristian Holm Nielsen for hjælp med forståelsen af PID.

1https://github.com/neic/Swagway

3

Indhold

Indhold | 4
1 Indledning | 5
2 Input | 5
3 Control | 12
4 Output | 14
5 Auxiliary | 21
6 Mekanik | 24
7 Konklusion | 24
8 Perspektivering | 24
Tabeller | 25
Figurer | 25
A Arbejdsdeling | 26
B Kildekode | 26
C Status log | 35

4

Swagway

1 Indledning

FiXme: indsæt pic
af swagway

Transport enheder bliver mere og mere avancerede, og der skabes oe nye enheder. Specielt mobilitet og anvendelighed har været i højsædet i mange nye produkter. Det handler om hurtigt at kunne komme fra punkt a til punkt b, uden at det kræver større besvær. Derudover er løsninger som er intuitive at bruge også fremskreden, og et produkt som opfylder alle disse punkter er Segwayen. Den er hurtig, kræver næsten ingen erfaring at køre på og er lille. Man kan hurtigt suse fra en afdeling til anden.
Formålet med projektet er at bygge en motoriseret selvbalancrende tohjulet transportenhed. Det er en klon af en Segway som er et kommercielt produkt, der benyes af en lille skare af befolkningen nutildags. Kendetegnet ved Segwayen er, at de to hjul sidder på samme aksel, hvor elektronik og motorene sørger for at, selv med en fører, holde enheden i balance. Når en fører læner sig frem eller tilbage, kompenserer Segwayen ved køre i samme retning, for aer at balancere den. For at dreje enheden vipper føreren håntaget til den ene eller anden side, som man ønsker at dreje til. Segwayen kan købes for cirka halverdstusinde kroner, hvis man ønsker at eje sådan en.
Projektoplæget lyder:
Formålet er at bygge en balance robot på to hjul, en Segway klon. Minimums målet er at få roboen til at balancere. Dereer få den til at køre
og kunne styre den hvis tid og evner rækker til det.
Hovedeudfordringen er at holde enheden lodret. For at gøre dee skal man kende enhedens vinkel i forhold til lodret og omsæe denne vinkel til et signal til motorene. Når vinklen stiger driver motorene hjulene som så flyer enheden og brugerens tygdepunk ind over akslen igen. Det kan se som tre isolerede problemstillinger som passer ind i I-C-O-modellen:
Input Måle Swagwayens hældning i forhold til lodret
Control Omsæe vinklen til et signal til motorene.
Output Drive to motore baseret på signalet.
Projektet er udarbejdet ud fra mikrokontrolleren Arduino Uno, i programmet arduino. Mikrokontrolleren bliver programmeret via. programmet Arduino, som nærmest er i sproget C++ med et Arduino bibliotek. Da vi har modtaget undervisning i denne platform, har dee været det oplagte redskab at benye til løsningen af vores projekt.

2 Input

2.1 Sensor

Eer nogen research af andre køretøjer og mindre roboer med der fungerer på sammen måde, var det klart at gyroskoper og accelerometere kunne måle vinklen så hurtigt og præcist som det var krævet.

5

Swagway

Sensor hardware
Gyroskoper og accelerometere har indtaget forbrugerens produkter, og kortlægger allerede nu deres bevægelser. De faldende priser og faldene energiforbrug har gjort, at gyroskoper og accelerometere er langt mere tilgængelige for alle. Mobiltelefoner, spilkonsoller og kameraer kan nu måle hvordan du bevæger dig, og flere og flere enheder importerer også disse bevægelses sensorer, for at adskille sig fra de andre. Disse bevægelses sensorer er avancerede MEMS (mikroelektromekaniske systemer) teknologier, som inkoorpererer gyroskoper, accelerometere og kompas sensorer. I dee projekt har vi arbejdet med gyroskoper og accelerometere, som vi også
kender fra vores smartphones. Swagwayen skal, lige som en smartphone kan måle
om den står eller ligger ned, måle i hvilken vinkel den står i. | FiXme: Check om
| vi har forklaret at der er brug for begge komponenter
Gyroskop
Et gyroskop måler vinkelhastigheder, hvor hurtigt noget drejer om en akse. Hvis denne vinkelhastighed integreres over tid finder man vinklen som gyroskopet har flyttet sig. Problemet med at integrer gyroskopdata er, at pga. måleusikkerheder vil det målte nulpunkt drive væk fra det fysiske nulpunkt. Moderne gyroskoper er et mikroelektromekanisk system, også kaldet MEMS. Det betyder, at det både er en mekanisk og elektrisk funktion i et system. /fxnotehvordan fungerer MEMS i et gyroskop

Accelerometer
Et accelerometer kan måle accelerationer. Man kan med hjælp fra tangens og data fra to akser udregne den vinklen accelerometeret står i forhold til jordens tyngdekræ. Problemet med dee er at accelerometer måler alle accelerationer, ikke kun jordens tyngdekræ. Når Swagwayen fx accelerer, bremser eller køre over en sten bliver den udregnet vinkel forkert. Et accelerometer måler en bevægelse, som enten er forårsaget af tyngdekraen eller en bevægelse. Som set på figur 1 måles accelerationen i et moderne MEMS accelerometer ved en ændring i kapacitansen, c, som skyldes en ændring i massens, m, position. Kapasitansen fører til en ændring i spændingen, som hereer digitaliseres via ADC og kan benyes af en mikrokontroller som Arduinoen. Dee gøres for de tre akser x, y og z, og accelerationen kan nu måles i alle retninger.

IMU
For at løse problemet med at gyroskopet driver og problemet med at accelerometret ikke er nøjagtig når det bliver påvirket af andre accelerationer end tygdekraen kan man bruge begge sensorer sammen. Man bruger begge sensoreres data og samler dem i et filter. Se mere herom i sektion 3.2.
De fleste moderne accelerometere og gyroskoper kommer i små SMD pakker som er vanskelig håndlodde. Heldigvis er det forholdsvis let at få disse sensorer monteret på et breakoutboard. Eer at have kigget på andre Segway kloner og balanceroboer
faldt valget på en IMU fra Sparkfun. Se figur 2. En inertial measurement unit, IMU, er
en enhed som kombinere flere sensorer. IMUen fra Sparkfun et ADXL345 accelerometer og et ITG-3200 gyroskop. Accelerometret og gyroskopet er begge tre-akset. FiXme: tre-akset? Det giver IMUen seks frihedsgrader (DOF). Swagwayen skal dog kun bruge tre fri-

hedsgrader; to akser fra accelerometret og en fra gyroskopet, men IMUen med seks
frihedsgrader var det mindste med digital interface.

6

Swagway

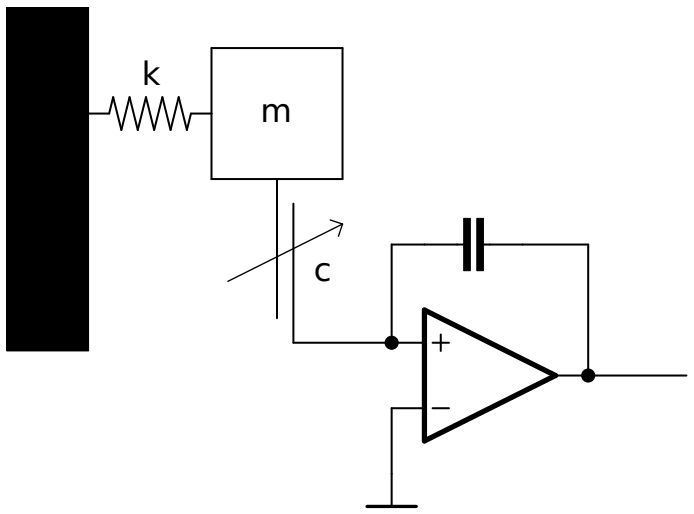
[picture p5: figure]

Figur 1: Et accelerometers interne MEMS-struktur

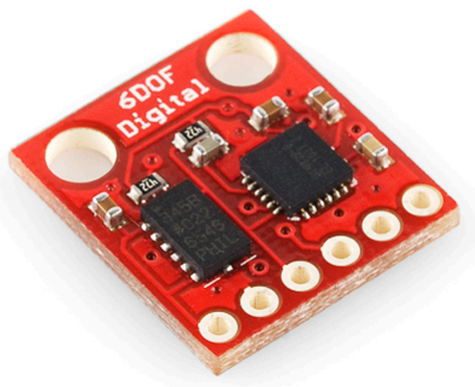
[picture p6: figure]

Figur 2: 6DOF IMU breakoutboard fra Sparkfun. (CC BY-NC-SA 3.0, Sparkfun)

I²C
Kommunikation med IMUen sker digital over en I²C-bus. På bussen er der en master² og en eller flere slaves. I Swagwayen er Arduinoen master og accelerometeret og gyroskopet er begge slaves. I²C bussen består af to fysiske forbindelser, en serial data linje (SDA) og en clock (SCL). Alle enheder på bussen forbinder til disse to forbindelser. Linjerne er open-drain med eksterne pull-up modstande. Det vil sige at i hver enhed sidder der MOSFETer der trækker spændingen på linjen mod GND eer behov. De eksterne pull-op modstande trækker linjerne op igen. Se figur 3.
På Arduinoen er I²C SDA på A4 og SCL på pin A5 med indbygget pull-up modstande på 20 kΩ--50 kΩ. [?, s. 317] De er aktiveret som standard når man bruger Wire biblioteket.³

2Det er mulig at lave et multi-master opstilling hvis alle masterne understøer det.
3
For reference se linje 75 i utility/twi.c i Wire biblioteket.

7

Swagway

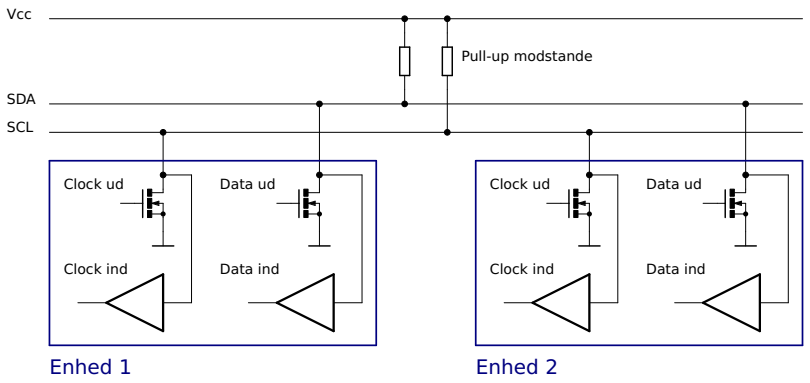
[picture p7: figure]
SDA; SCL; Clock ud; Clock ind; Data ind; Data ud; Vcc; Pull-up modstande; Enhed 1; Enhed 2

Figur 3: Eksempel på I²C-netværk

Arduinoens spænding er 5 V og IMUens er 3.3 V. IMUen bliver forsynet med 3.3 V fra Arduinoen, men SDA og SCL er koblet direkte til Arduinoens pins som har 5 V som reference. Den korekte løsning ville være at lave en level-shier imellem en 5 Vog en 3.3 V-del af I²C-bussen, men når pull-up modstandene er så høje som de er det stadig forsvarligt at kører IMUen direkte med 5 V som VIO-reference. Der er flere eksempler på det samme blandt andre på Interneet der bruger samme chips.
Den læeste måde at kommunikere over I²C fra en Arduino er at bruge Wirebibliotektet som kommer sammen Arduino-sowaren: #include <Wire.h> For at få Arduinoen til at tilslue sig bussen som master kaldes Wire.begin(); uden parametere. Slaverne på I²C-bussen har alle en adresse som fremgår af deres respektive datablade.
ADXL345 og ITG-3200 indeholder begge flere register med forskellige funktioner. Nogle registre indeholder opsætningen for chippen, andre indeholder det data som chippen måler. Hvis man, fra Arduinoen, vil skrive til et af registrene køre man følgene kode:
1 | Wire.beginTransmission(deviceAddress); | // begynder en
| session med enheden med deviceAddress
2 | Wire.write(regAddress); // sender adressen på den register
| man vil ændre
3 | Wire.write(value); // sender værdien registeren skal indtage
4 | Wire.endTransmission(); // afslutter sessionen
At læse et register er lidt mere omfaende:
1 | Wire.beginTransmission(deviceAddress); // begynder en session
| med enheden med deviceAddress
2 | Wire.write(regAddress); // sender adressen på den register man
| vil ændre
3 | Wire.endTransmission(); // afslutter sessionen
4

8

Swagway

5 Wire.beginTransmission(deviceAddress); // begynder en ny session
6 Wire.requestFrom(deviceAdress , numberOfBytes); // sender anmodning på at modtage numberOfBytes
7 | int i = 0;
8 | while (Wire.available()) { // så længe der er data tilgæ
ngeligt
9 | buffer[i] = Wire.read(); // modtag data og fyld det i buffer
10 | i++;
11 | }
12 | Wire.endTransmission(); // afslutter sessionen
Disse to funktioner bliver senere refereret til som hhv. writemem() og readmem().
FiXme: skriv om
hvad registerne
kan IMU biblioteker
I begyndelsen af projektet var alt kommunikationen med ADXL345 og ITG-3200 programmeret i swagway.ino. Det virkede og Arduinoen modtog data fra IMUen, men koden var svær at vedligeholde og gik tit i stykker. Der var desuden en fejl igennem lægere tid der resulterede i at den vinkel der blev udregnet fra gyroskopet, gyroAngle, var ca. dobbelt så stor som den burde være.#20 (https://github.com/neic/Swagway/issues/20) Eer mange ufuldendte forsøg på at ree fejlen blev alt gammel kode der var releateret til I²C sleet. Der blev istedet brugt et bibliotek passende til gyroskopet hvor alle funktioner var implementeret. Biblioteket hedder itg3200.
Det var ikke til at finde et ligende bibliotek til accelerometret, så med inspiration fra itg3200-bibliotekt blev der skrevet et. Biblioteket består af to filer. En headerfil, ADXL345.h, og selve funktionaliteten, ADXL345.cpp.
Headerfilen indeholder først definitioner på konstanter som enhedsadressen og registere:

23 #define ADXL345_ADDR_SD0_HIGH 0x1D
24 #define ADXL345_ADDR_SD0_LOW 0x53
25
26 // Registers
27 #define BW_RATE | 0x2C // RW SETUP: Output rate and low
power mode
28 #define POWER_CTL | 0x2D // RW SETUP: Power control
29 #define INT_SOURCE | 0x30 // R | INTERRUPT: Status
30 #define DATA_FORMAT | 0x31 // RW SETUP: Self -test and data
format
31 #define DATAX0 | 0x32 // R | SENSOR: Data
32
33 // Bitmaps
34 #define STANDBY_MODE | 0x00 // 0000 0000
35 #define MEASURE_MODE | 0x08 // 0000 1000
Værdierne og navnene er hentet ud fra databladet til ADXL345. [?] At have definitioner på alle konstanter gør koden læere læselig, så man ikke skal søge referencer i databladet.
Eerfølgene er der defineret en klasse med alle funktioner relateret til accelerometeret:

37 class ADXL345
38 {

9

Swagway

39 | public:
40 | float scaleFactor[3];
41 | float voltage;
42
43 ADXL345();
44
45 void init(unsigned int address); 46
47 | // SETUP: Mode
48 | void setStandbyMode();
49 | void setMeasureMode();
I ADXL345.cpp er funktionalitet skrevet. Som eksempel er her tre af de første funktioner er begge til opsætning af accelerometret.

setMeasureMode()

33 void ADXL345::setMeasureMode()
34 {
35 writemem(POWER_CTL , MEASURE_MODE);
36 }
setMeasureMode() skriver til power control registret, POWER_CTL. Funktionaliteten af
POWER_CTL er beskrevet i [?]. POWER_CTLs adresse er, som tidligere beskrevet, defineret FiXme: fix ref i ADXL345.h. MEASUREMODE er en sekvens af oe bits (en byte) somm hvis de skrives

i POWER_CTL, vil sæe accelerometret i måle tilstand. Sekvensen er ligledes udledt af
[?]. Den er i dee tilfælde 0000 0000 | FiXme: fix ref

FiXme: opdater
sekvensen

getOutputRate()

38 byte ADXL345::getOutputRate()
39 {
40 | readmem(BW_RATE , 1, &_buff[0]);
41 | return(_buff[0]);
42 }
getOutputRate() læser registret BW_RATE, ligger dataene i en buffer og retunerer aflæsningen.
setFullRes()

56 void ADXL345::setFullRes(bool _fullRes)
57 {
58 | readmem(DATA_FORMAT , 1, &_buff[0]);
59 | writemem(DATA_FORMAT , ((_buff[0] & ~(1 << 3)) | (_fullRes <<
| 3)));
60 }
setFullRes() skal kun ændre en bit i registret DATA_FORMAT. For at bebeholde de andre bits læser den først det som står i registret og gemmer det i en buffer. 1 << 3 betyder en bit shiet tre pladser til venstre: 00001000. ~(1 << 3) er Bitwise NOT værdien af dee: 11110111. Det bliver AND med bufferen, (_buff[0] & ~(1 << 3)) . Det er lig med alle de bit som er sat i bufferen pånær den erde sidste. Altså: den sæer den erde sidste bit til 0 og bibeholder alle andre. (_fullRes << 3) er værdien der skal sæes shiet tre pladser til venstre: 0000x000. Disse to værdi bliver til slut OR

10

Swagway

med hindanden og den erde sidste bit er nu ændret til værdien af _fullRes uden at nogle andre bits bliver ændret. Denne værdi bliver nu skrevet tilbage i samme buffer. To andre eksempler på funktionaliteten af ADXL345.cpp. Disse funktioner har med modtagelse af data at gøre.
isRawDataReady()

75
76 bool ADXL345::isRawDataReady()
77 {
78 | readmem(INT_SOURCE , 1, &_buff[0]);
79 | return(_buff[0] >> 7);
Accelerometeret har et register med interrupt flag, INT_SOURCE. isRawDataReady() læser dee register og gemmer det i en buffer. Bufferen bliver shiet syv pladser til højre og isRawDataReady() retunere en bool værdi alt eer om interrupt flaget er sat.
readAccRaw()

99 void ADXL345::readAccRaw(int *_AccX , int *_AccY , int *_AccZ) 100 {
101 | readmem(DATAX0 , 6, &_buff[0]);
102 | *_AccX = _buff[1] << 8 | _buff[0];
103 | *_AccY = _buff[3] << 8 | _buff[2];
104 | *_AccZ = _buff[5] << 8 | _buff[4];
105 }
Dataende i accelerometeret fylder seks registre af 8 bit. Hver akse fylder to registre hvoraf det første er den mindst betydene. readAccRav() læser DATAX0 og seks registre frem. Dataene bliver lagt i et buffer-array. Den mest betydene af de to bytes som høre sammen bliver shiet 8 pladser til venstre og dereer AND med den mindst betydene. De to bytes bliver sat sammen direkte eer hindanden. Værdierne bliver retuneret til tre integer-pointers.
2.2 Styring

Styringen af Swagwayen skulle være en længerevarende og holdbar løsning. Det ønskes ikke, at enheden eer forholdsvis kort tid skulle udskies eller repareres. Vi overvejede fem forskellige løsninger: En lineær potentiometer, et drejepotentiometer, gaffelsensor, strain-gate og stepper motor.

Lineær potentiometer

FiXme: billede af
linæert
potentiometer
fig:linpot

Et lieært potentiometer fungerer som et normalt potentiometer, dog trækkes "armen"i en sliske som set på figur ⁇ Potentiometret skal placeres i bunden af stangen, hvoreer potentiometrets arm trækkes med stangens bevægelse. Hereer vil man kunne ændre på PWM signalet til motorene, og på den måde dreje. Løsningen er
simpel at udføre, og vil virke let i praksis.
Ulempen ved denne løsning er dog, at potentiometret hurtigt slides op ved brug,
og det er derfor ikke en holdbar løsning. | FiXme: wut?

Dreje potentiometer
Samme princip fra det lineæere potentiometer gælder her. Derimod drejes dee potentiometer i stedet for om sin egen akse. Ideen med dee var, at man let kan imple-

11

Swagway

mentere den i toppen af Swagwayens styr, og så styre PWM signalet til motorerene sådan.
Lige som det linæere potentiometer, slides denne løsning hurtigt, og er derfor ikke holdbar. Derudover er denne løsning ikke lige så intuitiv og føles klodset, hvilket ikke er det vi ønsker med produktet.

Gaffelsensor
Gaffelsensorer benyes i gamle kuglemuse, som vi alle nok kender. Gaffelsensorene måler hvor meget noget har flyet sig ved at analysere bevægelsen i forhold til nogle bånd buede bånd, i to krysende retninger. Ud fra bevægelsen kan gaffelsensoren bestemme, hvordan kuglen har bevæget sig i dens socket. En lignende anordning kunne placeres i bunden af stangen lige som det lineæere potentiometer, og en kugle kunne skubbes rundt lige som i en mus, for at bestemme stangens hældningen. Løsningen er meget præcis hvis den er lavet mekanisk godt.
Gaffelsensoren er derimod ekstremt upræcis hvis mekanikken ikke er rentskåretnæsten perfekt. Yderligere bliver dens præcision påvirket af støv og skidt, hvilket hurtigt vil ophobe sig i bunden af vores Swagway.

Strain-gate
En strain-gate løsning er en anordning, som placeres på siden af stangen. Straingaten kan mærke tryk i metallet, og kan ud fra dee tryk bestemme en værdi, som man kan bruge til at styre Swagwayen med. Denne løsning er ekstrem præcis, og benyes oe i store maskiner.
Problemet er dog, at den ikke virker på vores stang, da den er for stiv, og løsningen hverken er intuitiv eller responsiv for forbrugeren. Den er ikke lige til at finde ud af fra første øjekast, og den er sværere at lære.

Stepper motor
Det sidste løsningsforslag: Stepper motor. Planen med denne var at foretage den modsae funktion af hvad man normalt gør med en stepper motor: I stedet for at få motoren til at bevæge noget, skal styret bevæge motoren, hvoreer det måles hvilket step den er på i Arduinoen. Løsningen er ekstremt robust og præcis, som vi kender stepper motorer for. Derudover vil den ikke være modtagelig for omgivelsernes påvirkninger i form af støv eller andet snavs. Yderligere kan steppene geares, så den bliver endnu mere præcis hvis nødvendigt.
Det sværeste ved denne løsning er, at implementere den.
Hvis tiden havde rækket til det, havde vi derfor valgt denne som den umiddelbare løsning.

3 Control

3.1 Hoved loop()

FiXme: Skriv om 3.2 Filter | main loop

Målet med filtret er at samle dataen fra gyroskopet, accelerometeret og ud fra disse
beregne en vinkel, som vi kan benye til at regulere PWM eer. Ud fra dee mål,

12

Swagway

udvalgte vi tre filtre, som har de egenskaber vi leder eer.

Komplementær filter
Det komplementære filter er kendetegnet ved, at det er let at sæe op, fordi det er meget intuitivt. Filtret hjælper også kraigt på støj og driing. Derudover er det hurtigt, hvilket betyder at Arduinoen kan beregne vinklen i nærmest real-time. Filtret består af et lav pas filter på accelerometeret, som kun lader længerevarende ændringer igennem, hvilket erner de problemer accelerometeret har med bevægelses-acceleration. Gyroskopets data passerer igennem et høj pas filter, som erner længerevarende ændringer. De længerevarende ændringer som gyroen er udsat for er driing. Når de to svagheder er reduceret kraigt vha. det komplementære filter, ender man med en vinkel der ligger meget nær virkeligheden.

Kalman filter
Kalman filtret er et professionelt filter, som benyes i de fleste køretøjer nutildags, da dee filter er yderst præcis. Kalman filtret er desværre også ekstremt svært at forstå, men fungerer i princippet lige som det komplementære: Det erne støj fra de to enheder, og reducerer kraigt deres ulighed. Kalman filtret er klart det bedste da den selv korrigerer dens gain med tiden - den lærer jo længere tid den kører. Desværre kræver Kalman filtret en ekstraoordinær viden inden for matematik.

3.3 Regulering

For at kontrolere hvorledes Swagwayens motorer bevæger sig i forhold til vinklen, skal vi bestemme et forhold mellem vinklens hældning og PWM.

Lineær
Den simpleste og mest basale reguleringsteknik til at holde Swagwayen i balance er et lineært filter. Her mappes PWM mellem et og treddive, hvoreer den forøges med en, hver gang vinklen stiger med en i den ene eller anden retning. Swagwayen vil derfor stige lineært i hastighed med den vinkel som den hælder med.
Den lineære regulering fungerer fint uden en fører eller med andet formål end blot at balancere.

PID
Proportional-Integral-Differential kontroller er en loop feedback mekanisme. PID kontrollerer en stor del af industrielle kontrolsystemer, da det er en feedback controller: Den beregne en "fejl"som er forskellen mellem den ønskede handling og den udførte. PID kontrolleren forsøger hereer at minimere fejlen ved at justere på kontrol input. PID forsøger derfor at opretholde eks. vinklen konstant ved det ønskede, ved hele tiden at justere sig selv.
PID er delt op i tre dele: Et proportionalt gain KP, som ganges med fejlen i systemet. Integralet af fejlen over tid, som ganges med KI

, for at erne fejlen omkring nul punktet, også kaldet steady-state. Differentialet af hvor hurtig fejlen ændrer sig, ganges med KD. Hvis der sker en hurtig ændring, bliver KD meget stor for at kompensere.

13

Swagway

Disse tre dele gør op for PID, som sørger for, at fejlen justeres lige meget hvilken
måde den ændres.
Vi startede med at implementere PID til at regulere den, men erfarede hurtigt at
det ikke virkede. For at PID virker, er det vigtigt at den fejl man beregner, stammer FiXme: insert old code fra kilden. Eer som vi ikke havde encodere på motorene kunne vi ikke bestemme
hvordan motorene reagerede. Så i stedet for at beregne forskellen mellem den ønskede handling og den udførte, beregnede vi forskellen mellem den ønskede handling
og den handling PWM signalet sendte. Da tiden var ved at løbe ud, bestemte vi os
for at lade PID og encoderne ligge, og gå videre til en ny løsning.

Eksponentiel
I stedet for PID introducerede vi en eksponentiel funktion. Den eksponentielle funktion får PWM signalet til at stige som en normal eksponentiel funktion stiger. Variablerne som funktionen er opstillet eer er fundet ud fra trial and error princippet. Nedenfor ses implementationen af reguleringen:

54 // PID
55
56 const int targetAngle = 0;
57 const float Ex = 2.6; //Exponential value 58 const float Kp = 2; //Proportional value

168 float pid(float input)
169 {
170 | float output;
171 | if (input >0)
172 | {
173 | output = pow(input ,Ex) + Kp*input;
174 | }
175 | else
176 | {
177 | output = -pow(-input ,Ex) + Kp*input;
178 | }
179 | return constrain(output , -255, 255);
180 }
Den eksponentielle funktion er den som sidder i det nuværende produkt. Vi kan med denne funktion køre på Swagwayen uden at falde, og den kan holde sin position uden at stå og "rykke"hårdt fra side til side.

4 Output

For at holde Swagwayen i balance, ønsker vi, ligesom Segwayen, at motorene skal kunne køre i begge retninger med en variabel hastighed.

4.1 H-broens virkemåde
FiXme: insert H H-broen bruges til kontrol af motore. En H-bro er fire kontakter sat op som et H, bridge pic med en motor i midten. Begge kontakter på en side må ikke være trykkede nede
samtidigt, så kører strømmen uden om motoren. Derudover må man ikke tænde for
de øverste motore samtidigt, for så kortsluer den. Hvis man derimod tænder for en

14

Swagway

af de øverste, og så den modsae nederste kontakt, bevæger motoren sig i den retning strømmen løber. Man tænder altså derfor H-broen i par af to modsae: Hvis den øverste til højre er tændt, tændes den nederste til venstre også, og hvis den øverste venstre tændes, tændes den nederste til højre også. Hele logikken kan findes på tabel ⁇.

4.2 PWM

Pulsbreddemodulation (Pulse-Width-Modulation): Er en metode til at kontrollere spændingen i elektriske apparater. Det er en metode til at levere spænding igennem en række impulser i stedet for der konstant er strøm igennem systemet. Ved at øge eller formindske bredden af impulsen kan man kontrollere en motor.
Man kan altså sige, at PWM er et on/off system hvor man styrer ved hurtigt, at slukke og tænde for spændingen. Tiden der går imellem at den er on/off er så kort, at en LED som sådan ikke mærker det. Så den vil ikke blinke, men derimod lyse mindre hvis man øger bredden imellem impulserne.
Måden vi styre dee på i en Arduino er via analogWrite(pin,…);. Her har vi mulighed for at give en værdi fra 0--255. Dee betyder at analogWrite(pin,255); er 100% og analogWrite(pin,127); er 50%. Dee kan også ses på figur 4.
FiXme: Hele
afsniet skal
omskrives
analogWrite(pin,0);
0%

analogWrite(pin,63);
25%

analogWrite(pin,127);
50%

analogWrite(pin,191);
75%

analogWrite(pin,255);
100%

Figur 4: Eksempel på PWM med varierende dutycycle

4.3 Overvejelser

Der er to muligheder under fremstilling af en H-bro. Enten kan der benyes en simpel H-bro chip, eller man kan fremstille en selv. Chippen er den nemme løsning, som gør alting super let at arbejde med. Dog kan chippen ikke håndtere store strømme, og det var derfor urealistisk at piggy-back dem.
Vi fremstillede derfor selv en H-bro, da den kan klare de store mængder af strøm vi arbejder med, selvom at det er langt mere komplekst og det forøger kraigt mængden af ting der kan gå galt.

15

Swagway

Eer som at motorene skal kunne køres med variable hastigheder, skal der køres PWM på disse. Man kan vælge, om dee skal ske i toppen eller bunden af H-broen som diskuteret før 4.1. Vi startede med at gøre dee i toppen, men dee blev senere ændret til bunden, hvilket er dybere beskrevet i motorcontroller v2.1. 4.4

4.4 Motorcontroller

Tabel 1: Motorcontroller v5.2 sandhedstabel
Arduino pin | HEXFET spænding | HEXFET on/off
P7 P6 | P5 | Q1 Q2 Q3 Q4 | Q1 Q2 Q3 Q4
P8 P9 P10 | Q5 Q6 Q7 Q8 | Q5 Q6 Q7 Q8
0 | 0 | 0 | 0 | 1 | 0 | 0 | 0 | 0 | 0 | 1 | Off (⟳)
1 | 0 | 0 | 0 | 0 | 0 | 1 | 0 | 1 | 0 | 0 | Off (⟲)
0 | 1 | 0 | 1 | 1 | 0 | 0 | 1 | 0 | 0 | 1 | ⟳
1 | 1 | 0 | 1 | 0 | 0 | 1 | 1 | 1 | 0 | 0 | Short
0 | 0 | 1 | 0 | 1 | 1 | 0 | 0 | 0 | 1 | 1 | Short
1 | 0 | 1 | 0 | 0 | 1 | 1 | 0 | 1 | 1 | 0 | ⟲
0 | 1 | 1 | 1 | 1 | 1 | 0 | 1 | 0 | 1 | 1 | Short
1 | 1 | 1 | 1 | 0 | 1 | 1 | 1 | 1 | 1 | 0 | Short
Tabellen viser hvordan den seneste motorcontroller, v5.2, opføre sig hvis den får inpuet angivet under “Arduino Pin”

H-bro, PWM, PWM-kondensator, beskyelses dioder, 4000 serie, optocopler

Samlet board
Det var upraktisk at have alle funktioner på samme board. H-broerne og optocouplerne blev flyet på sit eget board “Motorcontroller v1.0”.

Motorcontroller v1.0
FiXme: lav board
date til margin
note
24. januar 2012

FiXme: Indsæt
diagram over
Motorcontroller
v1.0
FiXme: Indsæt
figur over
Motorcontroller
v1.0

Det var der galt
Boardet virkede ikke. Det opførte sig som det var kortsluet. Det viste sig, at eer boardet var skilt helt af igen, at det plus tegn der skulle vise polariteten var sat ved den forkerte pol. Printet havde taget skade af at blive loddet på flere gange.
Der var desuden nogle af ledningene for tætsiddene og loddeøerne var lidt underdimensionerede. Der manglede også en mulighed for at se, hvilken vej strømmen løber i H-broerne.

Det blev der rettet
Plus tegnet blev flyet over til den rigtige pol. Ledningerne blev flyet længere væk fra hinanden, og loddeøernes størrelser forøget.

16

Swagway

Motorcontroller v2.0
8. marts 2012

Det var der galt
Dee board blev aldrig lavet færdigt; Ledningerne omkring pinheaderen var for tæt
eer at loddeøeren blev forstørret. Diagram og figur over printet kan findes i bilag. FiXme: ref

Det blev der rettet
Loddeøerne blev gjort en smule mindre for at tillade ledningerners forbipasserend.

Motorcontroller v2.1
8 marts 2012

Det var der galt

FiXme: ref til
fig:mosch2.1 Boardet fungerede umiddelbart. Motoren kunne køre i begge retninger og farten kunne styres med PWM. Dog startede motoren på ca. 30% fart uintentionelt i den ene
retning. Ved at måle på PWM signalet fra mainboardet og signalet til motoren via. et oscilloskop, kunne problemet indskrænkes til at være på Motorcontrolleren.
Det viste sig eer megen debugging, at spændingen på gaten på P-kanal HEXFE-Terne (IRF4905) ikke gik HIGH lige så hurtigt som ventet. Der blev opstillet et forsøg
på et breadboard med en P-kanal HEXFET, en optocoupler og en Arduino, for at
gennemskue problemet. | FiXme: Indsæt
| diagram over forsøg med optocoupler og HEXFET

Forsøget viste, at når optocoupleren sad mellem HEXFETen og Arduinoen var
der en ubekendt kapacitet mellem HEXFETens gate og source. Figur 6 viser nederst
PWM signalet fra Arduinoen og øverst signalet på P-kanal HTXFETens gate, hvor man tydeligt kan se, at det tager en ubelejlig tid før signalet på gaten stiger.
Ved at sæe en mindre pull-up modstand på, kunne gaten aflades hurtigere, men det var ikke muligt at få den tilpas langt ned til at kunne styre motoren godt. Ved at erne optocoupleren og køre HEXFETens gate direkte fra Arduinoen eller ved erne HEXFETen og måle direkte på optocoupleren, var stigningstiden ≈ 0. Det var kun i kombination mellem HEXFETen og transistoren i optocoupleren, at stigningstiden ikke var ≈ 0.
Der blev forsøgt med en 4N25 optocoupler istedet for 4N35, og en BC547 istedet for optocoupleren; der var samme stigningstid.
Det har ikke været muligt, selv med hjælp fra vejleder, at forklare hvorfor denne kapacitet er der.
Problemet blev ikke løst, det blev bare gjort ubetydeligt: Istedet for at bruge en N- og en P-kanal HEXFET til at bestemme retning og køre PWM på de andre to Nog P-kanal HEXFETer, blev det lavet om til at begge P-kanal HEXFETer blev brugt til at bestemme retning og at N-kanal HEXFETerne bliver brugt at køre PWM. Det er ikke et problem at stigetiden på P-kanal HEXFETerne er langsom da de kun ændre sig når der skies retning og ikke med høj frekvens som ved PWM.
For ikke at tilføje flere optocouplere og bruge flere pins på Arduinoen blev der, på motorcontrolleren tilføjet to invertere.

17

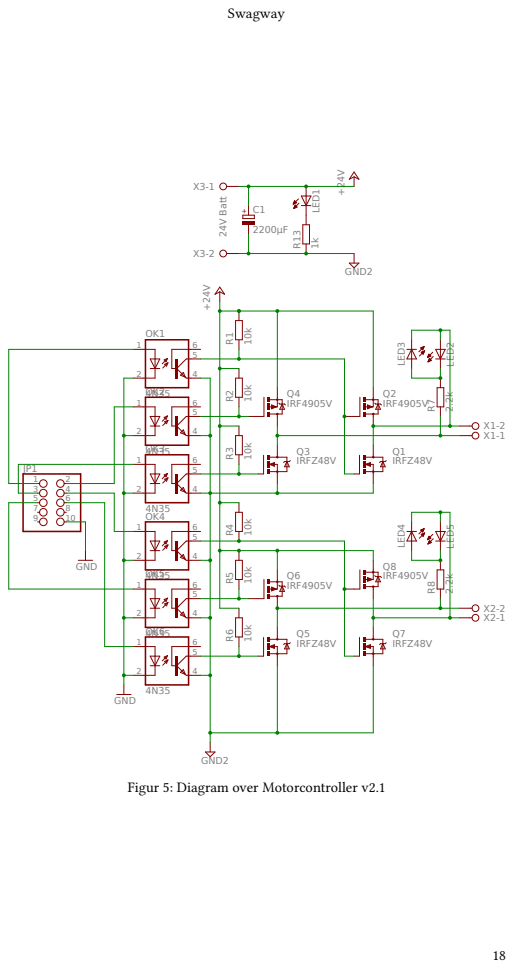
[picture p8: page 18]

Figur 5: Diagram over Motorcontroller v2.1

Swagway


Figur 6: Oscilloskop billede af stigetid på en P-kanal HEXFET gate. Nederst ses PWMsignalet fra Arduinoen, øverst ses signalet på HEXFETens gate.

Det blev der rettet
Vi byede om på to P- og N-kanal HEXFETer, så der nu køres PWM på N-kanalen, og P-kanalen bestemmer retning. Derudover blev det tilføjet to invertere på motorcon-
trolleren. Se figur | FiXme: ref:
| dia:v3.0
Motorcontroller v3.0
27. marts 2012

Det var der galt

| FiXme: Indsæt diagram over Motorcontroller v3.0 (Figur over printet kan findes i bilag)
Eer at der blev tilføjet en inverter på to af gatesne til P-kanal HEXFETerne er denne LOW når der ikke er spænding på optocouplerne (for eksempel når den ikke er koblet til mainboardet). Det tænder HEXFETen sammen med N-kanal HEXFETerne, som også er tændt uden spænding på optocouplerne, hvilket kortsluer H-broen. Motorcontroller v3.0 var fungerede, men det var upraktisk, at den var kortsluet uden at være koblet sammen med mainboardet.

Det blev der rettet
Pull-up modstandende blev derfor erstaet med pull-down modstande.

Motorcontroller v4.0
12. april 2012

19

Swagway

Det var der galt
Dee board blev aldrig lavet færdigt. En stor del af boardet blev re-routed da der var
blevet rodet eer mange versioner. Diagram og Figur over printet kan findes i bilag. FiXme: ref

Det blev der rettet
Boardet blev rerouted pga. rod.

Motorcontroller v4.1
13. april 2012

Det var der galt
Der var en ledning der ikke var routed og der var noget mindre re-routing.

Det blev der rettet
Reet op på fejl i routing

Motorcontroller v4.2
17. april 2012

Det var der galt
Dee board blev aldrig lavet færdigt. For-modstandene til optocouplerene sad på mainboardet af en ukendt årsag. Det virkede mere logisk og praktisk at have disse på motorboardet.

Det blev der rettet
For-modstandene til optocouplerne blev flyet fra mainboardet til motorcontrolleren.

Motorcontroller v5.0
24. april 2012

Det var der galt
Dee board blev aldrig lavet færdigt. Det er svært at debugge motorcontrolleren når man ikke kan se hvad der sker. Optocouplerenes manglende tegn på hvad der sker skabte problemer.

Det blev der rettet
Der blev tilføjet LEDer til optocouplerne.

Motorcontroller v5.1
24. april 2012

20

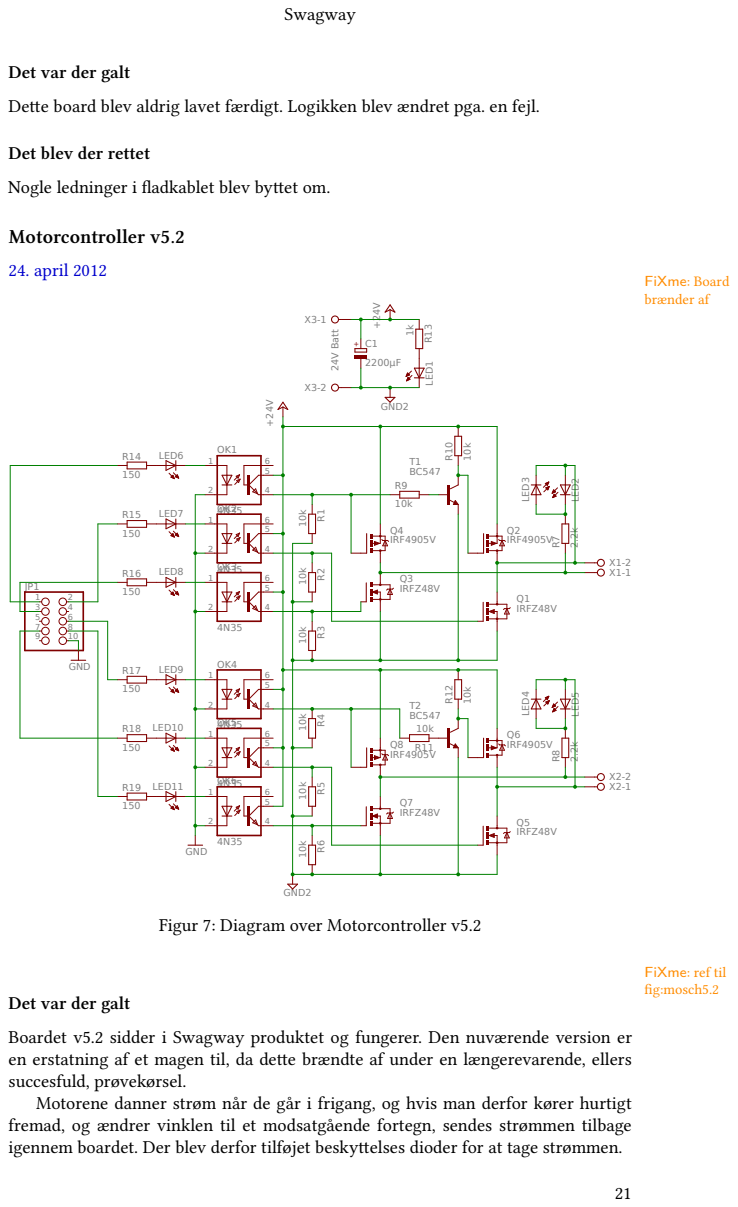
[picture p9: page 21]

Det var der galt
Dee board blev aldrig lavet færdigt. Logikken blev ændret pga. en fejl.

Det blev der rettet
Nogle ledninger i fladkablet blev byet om.

Figur 7: Diagram over Motorcontroller v5.2

Boardet v5.2 sidder i Swagway produktet og fungerer. Den nuværende version er
en erstatning af et magen til, da dee brændte af under en længerevarende, ellers
succesfuld, prøvekørsel.
Motorene danner strøm når de går i frigang, og hvis man derfor kører hurtigt
fremad, og ændrer vinklen til et modsatgående fortegn, sendes strømmen tilbage
igennem boardet. Der blev derfor tilføjet beskyelses dioder for at tage strømmen.

Swagway

Det blev der rettet
Der blev til v6.0 tilføjet beskyelses dioder til kredsløbet, for at tage strømmen fra motorene.

Motorcontroller v6.0
24. april 2012

5 Auxiliary

Tabel 2: Pin forbindelser på Arduino

Pin Forbindelse | Egenskaber
0 USB Rx
1 USB Tx
2 Radio Rx | Interrupt
3 | Interrupt, PWM
4 Radio Tx
5 Motorcontroller R2 PWMa
6 Motorcontroller L2 PWMa
7 Motorcontroller L1
8 Motorcontroller R1
9 Motorcontroller L3 PWM
10 Motorcontroller R3 PWM
11 | PWM
12
13 | LED
A0
A1
A2 Steering
A3 Steering
A4 IMU I²C SDA | SDA
A5 IMU I²C SCL | SCL
a PWM outpuet fra disse er lidt højere end forventet. De drives af en anden timer.#42 (https://github.com/neic/Swagway/issues/42) Se under Mainboard 4.0 i sektion 5.1.

5.1 Mainboard

Mainboard v1.0
24 jan 2012

Det var der galt
Mainboardets loddeøer var underdimensioneret#1, (https://github.com/neic/Swagway/issues/1) hvilket betyder, at lodninger blev besværlige. Yderligere var det ikke til at komme til at trykke på resetknappen på

22

Swagway

Arduinoen, da shieldet dækkede over knappen.#2 (https://github.com/neic/Swagway/issues/2)

Det blev der rettet
Der blev tilføjet en reset knap på mainboardet, i den følgende version. Der blev også tilføjet et stik til datamodtagning fra styringen på mainboardet.#12 (https://github.com/neic/Swagway/issues/12) Derudover blev loddeøerne udvidet.

Mainboard v2.0
1 marts 2012

Det var der galt
Logik kredsløbet blev kasseret. Eerfølgende blev der brugt tre Arduino pins per motor.#21 (https://github.com/neic/Swagway/issues/21) Display-boardet blev ligeledes kasseret.#9 (https://github.com/neic/Swagway/issues/9) Pinheaderne til 9V og IMUen var desuden for tæt sammen.#13 (https://github.com/neic/Swagway/issues/13)

Det blev der rettet
Pinheader til 9V baeri og IMU blev flet længere væk fra hinanden. Nyt logik implementeret.

Mainboard v3.0
26 marts 2012

Det var der galt
Dee board blev aldrig lavet færdig. På boardet blev der dog tilføjet pins til en radio, hvis formål er at kunne ændre reguleringsværdierne trådløst.#29 (https://github.com/neic/Swagway/issues/29)

Det blev der rettet
Mainboard v3.1
29 marts 2012

Det var der galt
For-modstandene var placeret på mainboardet, hvilket var ulogisk.#37 (https://github.com/neic/Swagway/issues/37) Pinheader til IMU passer med en 5×2 socket, men der er placeret en 7×2 på boardet.

Det blev der rettet
For-modstandene blev flyet fra mainboardet til motorcontrolleren. Pinheaderen til IMUen blev lavet om.

Mainboard v4.0
24 april 2012

23

Swagway

Det var der galt
Swagwayen kører med dee board, men den ene motor kørte hurtigere end den anden.#42 (https://github.com/neic/Swagway/issues/42) Det lignede umiddelbart en mekanisk fejl, men ved at bye om på ledningerne til motorene viste det sig at den ene kanal på motorcontrolleren kørte langsommere end den anden. Problement blev isoleret til, at Arduinoen ikke sendte PWM med samme frekvens til begge kanaler. I Arduino referencen for AnalogWrite() ser man også, at pin 5 og 6 PWM kører fra en anden timer end de andre PWM pins. Tilfældigvis kørte den ene motor på begge af disse pins.

Det blev der rettet
Pin 5 og 9 blev byet så Swagwayen kører lidt hurtigere forlæns end baglæns, men med samme forskel på begge hjul.
Ombytningen af de to pins blev gjort ved at bryde kobberbanerne på printet og lodde to ledninger på, der blev ikke lavet et nyt board.

6 Mekanik

FiXme: Skriv om
Motorer, baerier,
etc. 7 Konklusion

Vores mål var at lave en balance robot, hvor vi havde tilvalgt at lave styring til begge sider, hvis tiden rækkede til det.
Swagwayen fungerer som den står idag, og kan balancere på egen hånd. Det viste sig, at lave styring så den kunne dreje var i overkanten af hvad vi kunne nå inden for den givne tidsramme, hvori vi dog opfyldte vores minimumskrav. Swagwayen kan også køre frem og tilbage med en fører.

8 Perspektivering

Som nævnt i projektbeskrivelsen, ville vi gerne med mere tid, have ha implemente-
ret styring til Swagwayen. Kraigere motorer med mindre gearkasser. Encodere | FiXme: her
| mangler noget

24

Tabeller

1 | Motorcontroller v5.2 sandhedstabel | 16
2 | Pin forbindelser på Arduino | 22

Figurer

1 | Et accelerometers interne MEMS-struktur | | 7
2 | 6DOF IMU breakoutboard fra Sparkfun | | 7
3 | Eksempel på I²C-netværk | | 8
4 | Eksempel på PWM med varierende dutycycle | 15
5 | Diagram over Motorcontroller v2.1 | 17
6 | Oscilloskop billede af stigetid på en P-kanal HEXFET gate | 18
7 | Diagram over Motorcontroller v5.2 | 21

25

Swagway

A Arbejdsdeling

FiXme: Tilføj A.1 Udvikling | arbejdsdeling

A.2 Praktisk

A.3 Skriligt

B Kildekode

B.1 swagway.ino

1 /*************************************************/
2 /* swagway.ino -- Swagway onboard software | */
3 /* | | */
4 /* Author: Mathias Dannesbo <neic@neic.dk> and | */
5 /* | Carl -Emil Grøn Christensen | */
6 /* Time -stamp: <2012-05-07 18:07:19 (neic)> | */
7 /* Part of the Swagway project | */
8 /* https://github.com/neic/Swagway | */
9 /* | | */
10 /*************************************************/ 11
12 #include <Wire.h>
13 #include <math.h>
14 #include "ITG3200.h"
15 #include "ADXL345.h"
16
17 // IMU
18 ADXL345 acc = ADXL345(); 19 float accSampleRate;
20 ITG3200 gyro = ITG3200(); 21 float gyroSampleRate;
22
23 // General
24 int xa, ya, za;
25 float xg, yg, zg;
26
27 unsigned long sinceLastSend; 28
29 bool newAccData , newGyroData;
30
31 double accAngle , gyroAngle , estAngle;
32
33 // Kalman filter
34 const float Q_angle = 0.001; // Process noise covariance for
| the accelerometer - Sw
35 const float Q_gyro = 0.003; // Process noise covariance for the
| gyro - Sw
36 const float R_angle = 0.03; // Measurement noise covariance -Sv

26

Swagway

37
38 double angle = 0; // It starts at 0 degrees 39 double bias = 0;
40 double P_00 = 0, P_01 = 0, P_10 = 0, P_11 = 0; 41 double dt, y, S;
42 double K_0, K_1;
43
44 // Motor
45
46 const int directionPinLeft = 7; //HIGH when forward 47 const int forwardPinLeft = 9;
48 const int backwardPinLeft = 6;
49
50 const int directionPinRight = 8; //HIGH when forward 51 const int forwardPinRight = 10;
52 const int backwardPinRight = 5;
53
54 // PID
55
56 const int targetAngle = 0;
57 const float Ex = 2.6; //Exponential value 58 const float Kp = 2; //Proportional value 59
60 void setup()
61 {
62 | Serial.begin(115200);
63 | Wire.begin();
64
65 | //Init the acc
66 | acc.init(ADXL345_ADDR_SD0_LOW);
67 | acc.setFullRes(true);
68 | acc.setRange(3);
69 | acc.setVoltage(3.3);
70 | acc.setOutputRate(10); //25Hz*2^(10-8)=100Hz. See table 7 in
| ADXL345 datasheet
71
72 | //Calculate the accSampleRate
73 | accSampleRate = 25*pow(2,(acc.getOutputRate() -8)); //See
table 7 in ADXL345 datasheet 74
75 | //Init the gyro
76 | gyro.init(ITG3200_ADDR_AD0_LOW);
77 | gyro.setSampleRateDiv(79); //Set the sample rate to 8000Hz
| /(79+1)=100Hz
78
79 | //Calculate the gyroSampleRate
80 | if (gyro.getFilterBW() == BW256_SR8)
81 | {
82 | gyroSampleRate = 8000 / (gyro.getSampleRateDiv()+1);
83 | }
84 | else
85 | {
86 | gyroSampleRate = 1000 / (gyro.getSampleRateDiv()+1);
87 | }

27

Swagway

88
89 | pinMode(directionPinLeft , OUTPUT);
90 | pinMode(forwardPinLeft , OUTPUT);
91 | pinMode(backwardPinLeft , OUTPUT);
92 | pinMode(directionPinRight , OUTPUT);
93 | pinMode(forwardPinRight , OUTPUT);
94 | pinMode(backwardPinRight , OUTPUT);
95 | //Calibration
96 | gyro.zeroCalibrate(250,2);
97
98 | //Dump settings
99 | dumpIMUsettings();
100 }
101
102 void loop()
103 {
104 | if (acc.isRawDataReady())
105 | {
106 | acc.readAccRaw(&xa,&ya,&za);
107 | accAngle = atan2(xa,ya)*180/3.1415; // calcutalte the X-Y-
angle
108 | newAccData = true;
109 | }
110
111 | if (gyro.isRawDataReady())
112 | {
113 | gyro.readGyro(&xg,&yg,&zg);
114 | gyroAngle += zg/gyroSampleRate;
115 | newGyroData = true;
116 | }
117
118 | if (newAccData && newGyroData)
119 | {
120 | estAngle = kalman(accAngle , zg, micros()-sinceLastSend);
121 | // | sendToGraph();
122 | newAccData = newGyroData = false;
123 | float pwm = pid(estAngle);
124 | motorControl(pwm,pwm);
125 | Serial.print(estAngle);
126 | Serial.println(pwm);
127
128 | sinceLastSend = micros();
129 | }
130 }
131
132 | double kalman(double newAngle , double newRate , double dtime)
| {
133 | // KasBot V2 - Kalman filter module - http://www.arduino.cc
| | /cgi-bin/yabb2/YaBB.pl?num=1284738418 - http://www.x- firm.com/?page_id=145
134 | // with slightly modifications by Kristian Lauszus
135 | // See http://academic.csuohio.edu/simond/courses/eec644/
| | kalman.pdf and http://www.cs.unc.edu/~welch/media/pdf/ kalman_intro.pdf for more information

28

Swagway

136 | dt = dtime / 1000000; // Convert from microseconds to
| seconds
137
138 | // Discrete Kalman filter time update equations - Time
| Update ("Predict")
139 | // Update xhat - Project the state ahead
140 | angle += dt * (newRate - bias);
141
142 | // Update estimation error covariance - Project the error
| covariance ahead
143 | P_00 += -dt * (P_10 + P_01) + Q_angle * dt;
144 | P_01 += -dt * P_11;
145 | P_10 += -dt * P_11;
146 | P_11 += +Q_gyro * dt;
147
148 | // Discrete Kalman filter measurement update equations -
| Measurement Update ("Correct")
149 | // Calculate Kalman gain - Compute the Kalman gain
150 | S = P_00 + R_angle;
151 | K_0 = P_00 / S;
152 | K_1 = P_10 / S;
153
154 | // Calculate angle and resting rate - Update estimate with
| measurement zk
155 | y = newAngle - angle;
156 | angle += K_0 * y;
157 | bias += K_1 * y;
158
159 | // Calculate estimation error covariance - Update the error
| covariance
160 | P_00 -= K_0 * P_00;
161 | P_01 -= K_0 * P_01;
162 | P_10 -= K_1 * P_00;
163 | P_11 -= K_1 * P_01;
164
165 | return angle;
166 | }
167
168 float pid(float input) 169 {
170 | float output;
171 | if (input >0)
172 | {
173 | output = pow(input ,Ex) + Kp*input;
174 | }
175 | else
176 | {
177 | output = -pow(-input ,Ex) + Kp*input;
178 | }
179 | return constrain(output , -255, 255);
180 }
181
182 void motorControl(int left, int right) 183 {

29

Swagway

184 | if (left < 0)
185 | {
186 | digitalWrite(directionPinLeft , HIGH);
187 | digitalWrite(backwardPinLeft , LOW);
188 | analogWrite(forwardPinLeft , -left);
189 | }
190 | else
191 | {
192 | digitalWrite(directionPinLeft , LOW);
193 | digitalWrite(forwardPinLeft , LOW);
194 | analogWrite(backwardPinLeft , left);
195 | }
196 | if (right < 0)
197 | {
198 | digitalWrite(directionPinRight , HIGH);
199 | digitalWrite(backwardPinRight , LOW);
200 | analogWrite(forwardPinRight , -right);
201 | }
202 | else
203 | {
204 | digitalWrite(directionPinRight , LOW);
205 | digitalWrite(forwardPinRight , LOW);
206 | analogWrite(backwardPinRight , right);
207 | }
208 }
209 /* Serial communication */
210
211 void sendToGraph()
212 {
213 | Serial.print("<");
214 | Serial.print(gyroAngle); //0
215 | Serial.print(",");
216 | Serial.print(accAngle); //1
217 | Serial.print(",");
218 | Serial.print(estAngle); //2
219 | Serial.print(",");
220 | Serial.print(micros()-sinceLastSend); //3
221 | Serial.println(">");
222 }
223
224 void dumpIMUsettings()
225 {
226 | Serial.println();
227 | Serial.println("========================================");
228 | Serial.println("==============IMU Settings ==============");
229 | Serial.println();
230 | Serial.println(" | ---Gyro --- | ");
231 | Serial.print("Sample rate | (Hz) = ");
232 | Serial.println(gyroSampleRate ,0);
233 | Serial.println();
234 | Serial.println(" | ---Acc--- | ");
235 | Serial.print("Sample rate | (Hz) = ");
236 | Serial.println(accSampleRate ,0);
237 | Serial.print("Full resolution | = ");

30

Swagway

238 | Serial.println(acc.getFullRes());
239 | Serial.print("Range | (g) = ");
240 | Serial.println(pow(2,(1+acc.getRange())),0);
241 | Serial.print("Scale factor X | (LBS/g) = ");
242 | Serial.println(acc.scaleFactor[0],0);
243 | Serial.print("Scale factor Y | (LBS/g) = ");
244 | Serial.println(acc.scaleFactor[1],0);
245 | Serial.print("Scale factor Z | (LBS/g) = ");
246 | Serial.println(acc.scaleFactor[2],0);
247 | Serial.println();
248 | Serial.println("============end IMU Settings ============");
249 | Serial.println("========================================");
250 | Serial.println();
251 }
B.2 ADXL345.h

1 /*************************************************/
2 /* ADXL345.h -- ADXL345/I2C libary for Arduino | */
3 /* | */
4 /* Author: Mathias Dannesbo <neic@neic.dk> and | */
5 /* | Carl -Emil Grøn Christensen | */
6 /* Time -stamp: <2012-04-04 17:37:05 (neic)> | */
7 /* Part of the Swagway project | */
8 /* https://github.com/neic/Swagway | */
9 /* | */
10 /* Inspired by the ITG3200 Arduino library at | */
11 /* http://code.google.com/p/itg -3200driver | */
12 /*************************************************/ 13
14 #ifndef ADXL345_h
15 #define ADXL345_h
16
17 #if defined(ARDUINO) && ARDUINO >= 100 18 #include "Arduino.h"
19 #else
20 #include "WProgram.h"
21 #endif
22
23 #define ADXL345_ADDR_SD0_HIGH 0x1D 24 #define ADXL345_ADDR_SD0_LOW 0x53
25
26 // Registers
27 #define BW_RATE | 0x2C // RW SETUP: Output rate and low
power mode
28 #define POWER_CTL | 0x2D // RW SETUP: Power control
29 #define INT_SOURCE | 0x30 // R | INTERRUPT: Status
30 #define DATA_FORMAT | 0x31 // RW SETUP: Self -test and data
format
31 #define DATAX0 | 0x32 // R | SENSOR: Data
32
33 // Bitmaps
34 #define STANDBY_MODE | 0x00 // 0000 0000
35 #define MEASURE_MODE | 0x08 // 0000 1000

31

Swagway

36
37 class ADXL345
38 {
39 | public:
40 | float scaleFactor[3];
41 | float voltage;
42
43 ADXL345();
44
45 void init(unsigned int address); 46
47 | // SETUP: Mode
48 | void setStandbyMode();
49 | void setMeasureMode();
50
51 | // SETUP: Output Rate
52 | byte getOutputRate();
53 | void setOutputRate(byte _SampleRate);
54
55 | // SETUP: Data format
56 | bool getFullRes();
57 | void setFullRes(bool fullRes);
58 | int getRange();
59 | void setRange(int range);
60
61 | // INTERRUPT
62 | bool isRawDataReady();
63
64 | // SETUP: Data processing
65 | void setVoltage(float _voltage);
66 | void updateScaleFactor();
67
68 | // SENSOR: Read
69 | void readAccRaw(int *_AccX , int *_AccY , int *_AccZ);
70 | void readAcc(float *_AccX , float *_AccY , float *_AccZ);
71
72 | void writemem(uint8_t _addr , uint8_t _val);
73 | void readmem(uint8_t _addr , uint8_t _nbytes , uint8_t __buff
[]);
74
75 | private:
76 | uint8_t _dev_address;
77 | uint8_t _buff[6];
78 };
79
80 #endif /* ADXL345_h */
B.3 ADXL345.cpp

1 /*************************************************/ 2 /* ADXL345.cpp -- ADXL345/I2C libary for Arduino */
3 /* | | */
4 /* Author: Mathias Dannesbo <neic@neic.dk> and | */
5 /* | Carl -Emil Grøn Christensen | */

32

Swagway

6 /* Time -stamp: <2012-05-11 04:52:13 (neic)> | */
7 /* Part of the Swagway project | */
8 /* https://github.com/neic/Swagway | */
9 /* | */
10 /* Inspired by the ITG3200 Arduino library at | */
11 /* http://code.google.com/p/itg -3200driver | */
12 /*************************************************/ 13
14 #include "ADXL345.h"
15 #include <Wire.h>
16
17 ADXL345::ADXL345()
18 {
19 }
20
21 void ADXL345::init(unsigned int address) 22 {
23 | _dev_address = address;
24 | setStandbyMode();
25 | setMeasureMode();
26 }
27
28 void ADXL345::setStandbyMode()
29 {
30 writemem(POWER_CTL , STANDBY_MODE); 31 }
32
33 void ADXL345::setMeasureMode()
34 {
35 writemem(POWER_CTL , MEASURE_MODE); 36 }
37
38 byte ADXL345::getOutputRate()
39 {
40 | readmem(BW_RATE , 1, &_buff[0]);
41 | return(_buff[0]);
42 }
43
44 void ADXL345::setOutputRate(byte _rate) 45 {
46 | _rate %= 16; //Prevent overflow
47 | writemem(BW_RATE , _rate);
48 }
49
50 bool ADXL345::getFullRes()
51 {
52 | readmem(DATA_FORMAT , 1, &_buff[0]);
53 | return(_buff[0] >> 3);
54 }
55
56 void ADXL345::setFullRes(bool _fullRes) 57 {
58 readmem(DATA_FORMAT , 1, &_buff[0]);

33

Swagway

59 | writemem(DATA_FORMAT , ((_buff[0] & ~(1 << 3)) | (_fullRes <<
| 3)));
60 }
61
62 int ADXL345::getRange()
63 {
64 | readmem(DATA_FORMAT , 1, &_buff[0]);
65 | return(_buff[0] & B00000011);
66 }
67
68 void ADXL345::setRange(int range) 69 {
70 | range %= 4; //Prevent overflow
71 | readmem(DATA_FORMAT , 1, &_buff[0]);
72 | writemem(DATA_FORMAT , ((_buff[0] & ~3) | range));
73 }
74
75
76 bool ADXL345::isRawDataReady()
77 {
78 | readmem(INT_SOURCE , 1, &_buff[0]);
79 | return(_buff[0] >> 7);
80 }
81 void ADXL345::setVoltage(float _voltage) 82 {
83 | voltage = _voltage;
84 | updateScaleFactor();
85 }
86
87 void ADXL345::updateScaleFactor() 88 {
89 | int rangeScale=256;
90 | if (!getFullRes())
91 | {
92 | rangeScale = pow(2,(8-getRange()));
93 | }
94 | scaleFactor[0] = rangeScale*0.89013671875+rangeScale
| *0.0439453125*voltage;
95 | scaleFactor[1] = rangeScale*0.89013671875+rangeScale
| *0.0439453125*voltage;
96 | scaleFactor[2] = rangeScale;
97 }
98
99 void ADXL345::readAccRaw(int *_AccX , int *_AccY , int *_AccZ) 100 {
101 | readmem(DATAX0 , 6, &_buff[0]);
102 | *_AccX = _buff[1] << 8 | _buff[0];
103 | *_AccY = _buff[3] << 8 | _buff[2];
104 | *_AccZ = _buff[5] << 8 | _buff[4];
105 }
106
107 void ADXL345::readAcc(float *_AccX , float *_AccY , float *_AccZ) 108 {
109 int x, y, z;

34

Swagway

110 | readAccRaw(&x,&y,&z);
111 | *_AccX = x / scaleFactor[0];
112 | *_AccY = y / scaleFactor[1];
113 | *_AccZ = z / scaleFactor[2];
114 }
115
116 void ADXL345::writemem(uint8_t _addr , uint8_t _val) {
117 | Wire.beginTransmission(_dev_address); | // start transmission
| to device
118 | Wire.write(_addr); // send register address
119 | Wire.write(_val); // send value to write
120 | Wire.endTransmission(); // end transmission
121 }
122
123 void ADXL345::readmem(uint8_t _addr , uint8_t _nbytes , uint8_t
| __buff[]) {
124 | Wire.beginTransmission(_dev_address); // start transmission
| to device
125 | Wire.write(_addr); // sends register address to read from
126 | Wire.endTransmission(); // end transmission
127
128 | Wire.beginTransmission(_dev_address); // start transmission
| to device
129 | Wire.requestFrom(_dev_address , _nbytes);// send data n-bytes
| read
130 | uint8_t i = 0;
131 | while (Wire.available()) {
132 | __buff[i] = Wire.read(); // receive DATA
133 | i++;
134 | }
135 | Wire.endTransmission(); // end transmission
136 }

C Status log

C.1 13. marts

Mainbord er fungerende. v2.0 af motorboardet er næsten færdig.
Kredsløbet uden om printne er næsten færdig.
Vi kan læse data fra IMUen og vi har et halvt implementert kalman-filter. Eer kalmanfilteret fungere skal der implementeres PID med wrapper kode.

35

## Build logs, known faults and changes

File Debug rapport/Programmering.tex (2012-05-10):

\documentclass[a4paper,oneside,article,danish,table]{memoir}
\checkandfixthelayout
\XeTeXtracingfonts= 1
\usepackage{babel,microtype,verbatim,threeparttable,amsmath,amssymb,unicode-math,hyperref,siunitx,mhchem,tikz,pgfplots,tikz-timing}
\sisetup{per-mode=symbol}
\microtypesetup{final,verbose=silent}
\usetikzlibrary{mindmap,arrows,positioning,shapes}
\setmainfont[Ligatures={TeX}]{Arno Pro}
%\setmainfont{Linux Libertine O}
\setmathfont{[Asana-Math]}
%\hfuzz=1pt
\usepackage[margin,draft]{fixme}
\fxusetheme{color}

\newcommand{\authorvar}{Mathias~Dannesbo}
\newcommand{\pretitlevar}{Programmering~C~eksamen:}
\newcommand{\titlevar}{Swagway~Debugger} 
\newcommand{\subtitlevar}{0} 
\newcommand{\datevar}{\today} 
\newcommand{\subjectvar}{Programmering~C}
\newcommand{\classvar}{EUC Nord: HTX Frederikshavn, f11htx3.B}
\newcommand{\teachervar}{}

\makepagestyle{articlehead}
\makeevenhead{articlehead}{\authorvar}{\subjectvar: \titlevar\\\classvar}{\datevar}
\makeevenfoot{articlehead}{}{\thepage}{}
\makeoddhead{articlehead}{\authorvar}{\subjectvar: \titlevar\\\classvar}{\datevar}
\makeoddfoot{articlehead}{}{\thepage}{}
\pagestyle{articlehead}

\usepackage{listings,textcomp}
\lstset{language=[Sharp]C,
%  morekeywords={[2]abs,acos,asin,atan,atan2,ceil,constrain,cos,degrees,exp,floor,log,map,max,min,radians,random,randomSeed,round,sin,sq,sqrt,tan,bitRead,bitWrite,bitSet,bitClear,bit,highByte,lowByte,analogReference,analogRead,analogWrite,attachInterrupt,detachInterrupt,delay,delayMicroseconds,digitalWrite,digitalRead,interrupts,millis,micros,noInterrupts,noTone,pinMode,pulseIn,shiftIn,shiftOut,tone,Serial,Serial1,Serial2,Serial3,begin,end,peek,read,print,println,available,flush,setTimeout,find,findUntil,parseInt,parseFloat,readBytes,readBytesUntil},
  keywordstyle={\bfseries\color[rgb]{0,0,1}},
%  keywordstyle={[2]\bfseries\color[rgb]{0.8,0.33,0}},
  identifierstyle=\ttfamily,
  commentstyle=\color[rgb]{0.133,0.545,0.133},
  stringstyle=\color[rgb]{0.627,0.126,0.941},
  showstringspaces=false,
  basicstyle=\small\ttfamily,
  numberstyle=\footnotesize,
  numbers=left,
  stepnumber=1,
  numbersep=10pt,
  tabsize=2,
  breaklines=true,
  breakatwhitespace=false,
  upquote=true,
  extendedchars=true,
  literate={æ}{{\ae}}1
    {ø}{{\o}}1
    {å}{{\aa}}1
}

\newcommand{\form}[2]{\lstinputlisting[firstnumber=#1,firstline=#1,lastline=#2]{../Software/Form1.cs}}
\newcommand{\boarddate}[1]{\textcolor{blue!80!black}{#1}}
\newcommand{\issue}[1]{\textsuperscript{\textcolor{blue!80!black}{\href{https://github.com/neic/Swagway/issues/#1}{\##1}}}}

\begin{document}
% \includepdf{forside.pdf} \clearpage%------------------------ Forside

\begin{center}
  \if\pretitlevar 0
  \else{\Large\pretitlevar\\} \fi
  \textsc{\HUGE\titlevar\\}
  \if\subtitlevar 0
  \else {\Large\subtitlevar\\} \fi
  %\vspace{1em}
  {\LARGE 
  af\\
   \authorvar}\\
 \datevar\\
\end{center}
\begin{abstract}
This journal is a walk-through of the source code of Swagway Debugger, a Windows application for debugging and tuning Kalman-filters, on balancing robots and Segway clones. It is made as a part of the Swagway project.
\end{abstract}
\thispagestyle{empty}

\chapter{Indledning}
Formålet med opgaven er at lave et stykke software der kan bruges sammen med forfatterens eksamenprojekt i Teknikfag~A:~El. Formålet med teknikfags projektet er at bygge en Segway klon, en motoriseret selvbalancrende tohjulet transportenhed. Navnet på teknikfag~A-projektet er Swagway. Under udviklingen af Swagway blev der behov for et stykke software til at teste et filter.\footnote{Websiden for hele projekter findes på \url{https://github.com/neic/Swagway}. Derfra er der adgang til alt kildekode, rapporter og andre skriftlige fremstillinger.}

\subsubsection{Kort beskrivelse af Swagway funktion}
For at Swagway kan holde sig lodret skal den kende vinklen den er fra lodret. Det udregner den ved at læse data fra to sensorer: et accelerometer og et gyroskop.

Et gyroskop kan måle vinkelhastigheder. Det vil sige ændringer i vinklen. Hvis denne vinkelhastighed integreres over tid finder man vinklen gyroskopet har flyttet sig. Problemet med at integrer gyroskopdata er, at pga. måleusikkerheder vil det målte nulpunkt drive væk fra det fysiske nulpunkt.

Et accelerometer kan måle accelerationer. Man kan med hjælp fra tangens og data fra to akser udregne den vinklen accelerometeret står i forhold til jordens tyngdekræft. Problemet med dette er at accelerometer måler alle accelerationer, ikke kun jordens tyngdekræft. Når Swagwayen fx accelerer, bremser eller køre over en sten bliver den udregnet vinkel forkert.

For at komme begge problemer til livs bliver begge sensorer brugt og data fra begge to bliver samlet i et såkaldt Kalman-filter. Kalman-filtret kan tilnærmelsesvis ses som et high-pass og low-pass filter. Det taget de hurtige ændringer (high-pass) fra gyroskop-dataene og bruger accelerometer-dataene til at holde det målte og det fysiske nulpunkt ens.

\subsubsection{Swagway Debugger}
For at teste om Kalman-filtret er implementeret og tunet korrekt er det nødvendig at sammenligne de tre vinkler fra hhv. gyroskopet, accelerometeret og Kalman-filtret. En måde at gøre dette på er ved at sende disse data fra elektronikken på Swagwayen til en PC og vise dem grafisk. Det er her Swagway~Debugger-softwaren kommer ind i billedet.

Swagway~Debugger modtager data, over en seriel-port, fra en Arduino microcontroller på Swagwayen og skriver dataene på en graf. Som der står i produktbeskrivelsen:
\begin{quotation}
  Opgaven er at lave software der kan modtage data fra en Arduino over en serielport og visualiserer det. Softwaren er til test af filtereringen af data fra et gyroskop og accelerometer. Softwaren viser bl.a. et rullende plot, samt nogle viserinstrumenter.
\end{quotation}

\chapter{Udførelse}
Swagway~Debugger er skrevet på Microsoft Windows i C\# som en Windows Form Application. Der er ingen eksterne afhængighedder; det bruger kun Microsoft biblioteker:
\form{9}{12}
Der er fem globale variabler:
\form{18}{23}
De tre første er buffere der bliver brugt til midlertidig at gemme modtaget data i, de to sidste er tællere over antallet af pakker.

\section{Indstillinger}
\begin{figure}[htbp]
  \centering
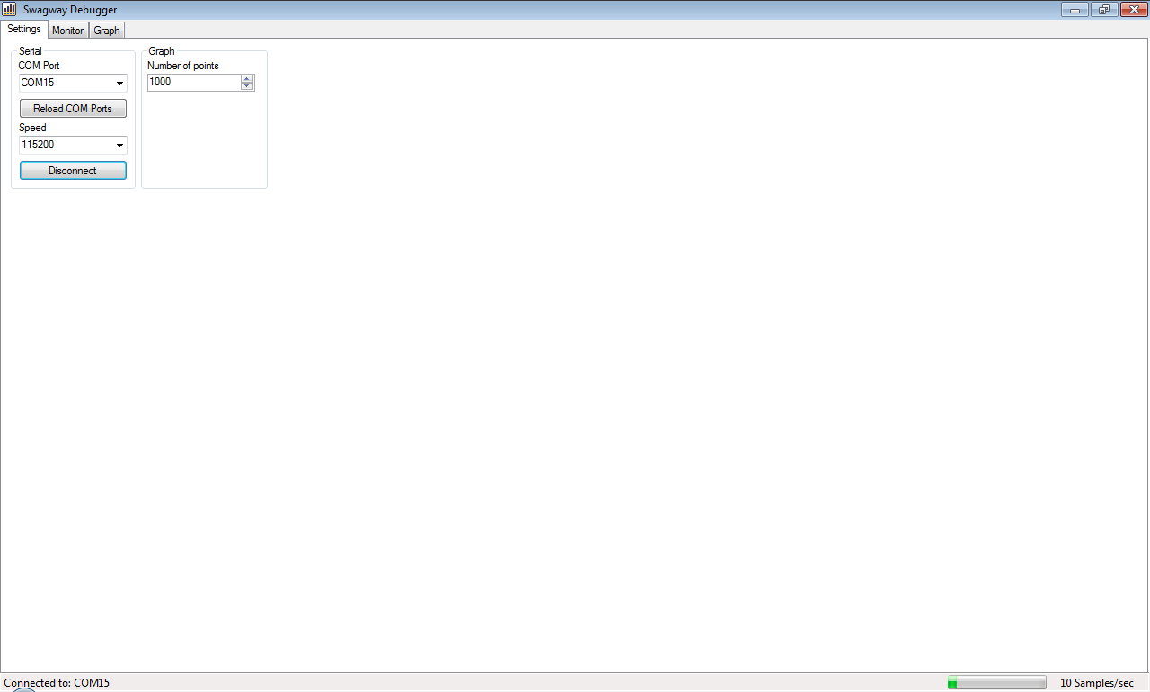
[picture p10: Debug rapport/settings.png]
  
  % \caption[]{}
  % \label{fig:}
\end{figure}
Ved opstart af applikationen indlæses alle tilgængelige serial-porte og der sættes en standardindstilling for valget af seriel hastighed:
\form{34}{39}
Ved afslutning af applikationen lukkes en eventuel åben seriel-port:
\form{41}{48}

\texttt{LoadSerialPorts()} kaldes ved opstart og ved tryk knappen \texttt{btReload}. Den føjer alle systemets serial-porte til listen, sætter den første seriel-port som standardindstilling og advare i statuslinjen hvis der ikke er fundet nogle seriel-porte:
\form{50}{68}

% btReload_Click undladt
Eventhandleren for \texttt{btConnect} både forbinder og afbryder til en seriel-port. Hvis der er afbrud finder den hvilken seriel-port og hastighed der er valgt, forbinder og opdaterer statuslinjen og dens egen tekst til “Disconnect”. Hvis der er oprettet forbindelse afbryder den og ligeledes opdaterer statuslinjen og dens egen tekst til “Connect”:
\form{76}{104}
NumericUpDown-tælleren, \texttt{udPackages}, bestemmer hvor meget data der skal vises på grafen. Når værdien i tælleren ændres ændre den dynamisk skala. Endeligt opdaterer den grafens X-akses maksimalværdi:
\form{106}{125}

\section{Seriel modtagelse og monitor}
\begin{figure}[htbp]
  \centering
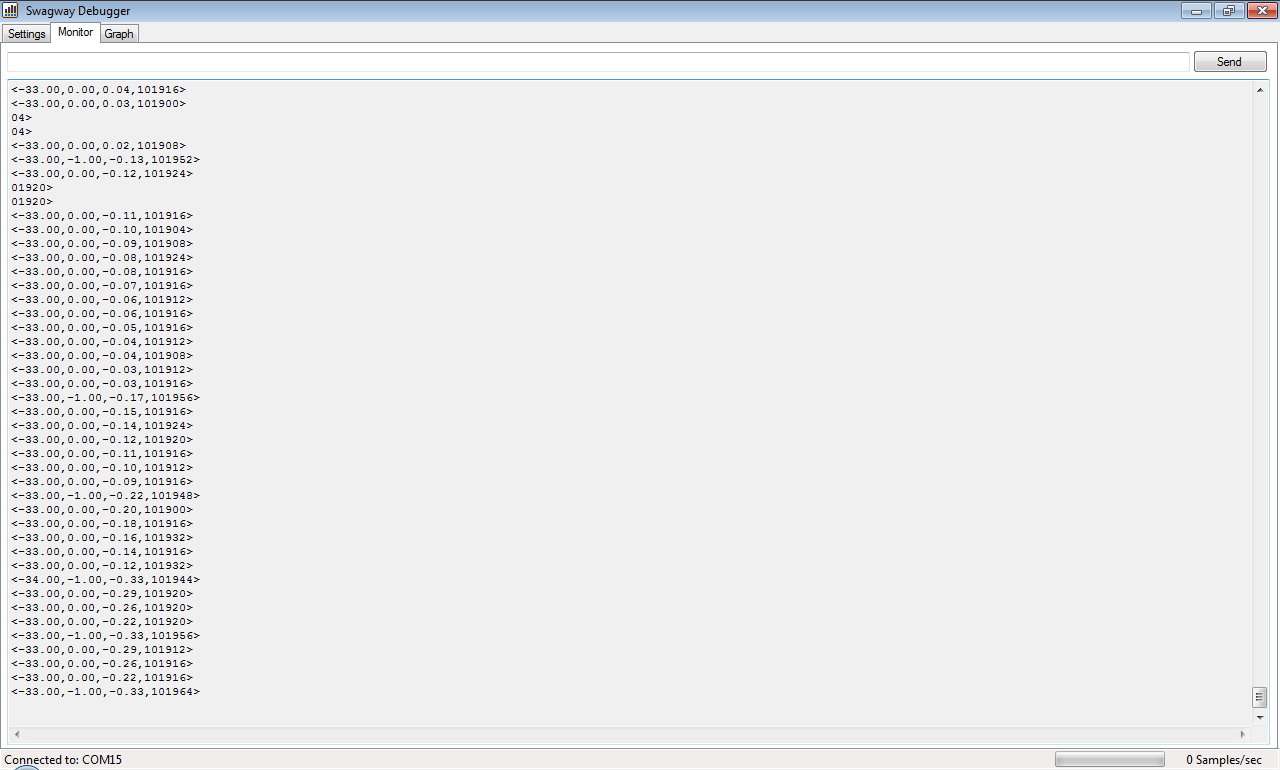
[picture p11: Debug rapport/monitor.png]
  
  % \caption[]{}
  % \label{fig:}
\end{figure}
Når der, efter der er forbundet til en seriel-port, ankommer data lægges det i bufferen \texttt{readFromUART} og \texttt{ReadToMonitor} kaldes:
\form{131}{136}
\texttt{ReadToMonitor} Skriver den modtaget data, \texttt{readFromUART}, direkte til monitoren uden at behandle den. Den undesøger om der er meget data i monitoren og sletter en smugle af det ældste hvis det er tilfældet. Til slut kalder den \texttt{CleanData()}.
\form{138}{149}
Datapakkerne fra Swagwayen er af formen $<\langle \text{gyro} \rangle,\langle \text{acc} \rangle,\langle \text{kalm} \rangle,\langle \text{tid} \rangle>$
\begin{tabbing}
H\=vor\\
\> $\langle \text{gyro} \rangle$ er vinklen målt med gyroskopet med to decimaler og eventuelt negativt fortegn,\\
\> $\langle \text{acc} \rangle$ er vinklen målt med accelerometeret med to decimaler og eventuelt negativt fortegn,\\
\> $\langle \text{gyro} \rangle$ er vinklen udregnet af Kalman-filtret med to decimaler og eventuelt negativt fortegn og\\
\> $\langle \text{tid} \rangle$ er tiden i \si{µS} siden sidste pakke blev sendt.
\end{tabbing}
\texttt{CleanData()} tager den rå modtaget data, \texttt{readFromUART}, og tilføjer det til en ny buffer, \texttt{rxStringBuffer}. Den indeholder allerede en rest data fra sidste gang. Denne buffer bliver splittet og hver pakke bliver indsat i listen \texttt{rxListBuffer}. Den sidste, ikke fuldstændige, pakke bliver lagt tilbage i \texttt{rxStringBuffer} og er klar til at bliver parret sammen ved næste kald af \texttt{CleanData()}:
\form{151}{157}
Pakkerne i \texttt{rxListBuffer} bliver renset for alt der står efter “>” og bliver undersøgt om de passer ind i formen for en pakke af en regular expression. Hvis den gør dette bliver pakken splittet til et array af \texttt{string}s for derefter at bliver parset til et array af \texttt{float}s. Dette array bliver givet vidre til til funktionen \texttt{plotPackage()}:
\form{159}{189}

Applikationen kan også sende data. Det er undladt af journalen. Se hvordan virker på linje 195--218 af Form1.cs.

\section{Graf}
\begin{figure}[htbp]
  \centering
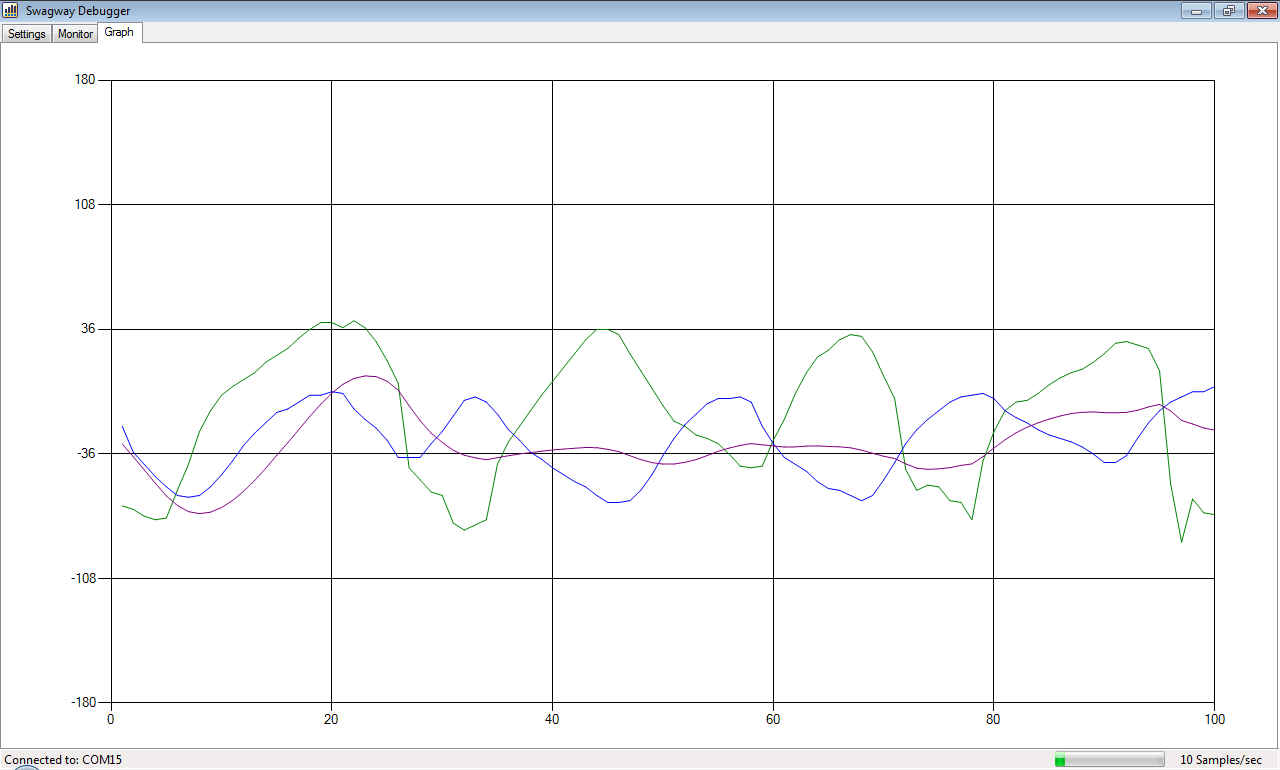
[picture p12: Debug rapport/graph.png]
  
  % \caption[]{}
  % \label{fig:}
\end{figure}
Når en ny pakke er blevet renset, bliver hver del af den tilføjet grafen i forskellige serier. Tiden bliver ignoreret. Der bliver så undersøgt om der er flere pakker end grænseværdien. Hvis der er det, bliver de fjernet fra grafen:
\form{224}{239}

\section{Statuslinje}
En timer kalder hvert sekund eventhandleren \texttt{timerSample\_Tick} undersøger hvor mange pakker der er tilføjet det sidste sekund. Den skriver antallet til statuslinjen og opdaterer en statusbjælke:
\form{245}{258}

\chapter{\texttt{Debug\_test.ino}}
Swagway projektet med gyroskopet og accelerometeret er afleveret, så for at teste Swagway Debugger er der lavet et lille test program til en Arduino. Til Arduinoen er der tilkoblet to potentiometerere til at simulere data fra gyroskop og accelerometer. Den del af softwaren som har interesse er den som sender pakken med data:
\lstset{language=[Visual]C++,
  morekeywords={[2]abs,acos,asin,atan,atan2,ceil,constrain,cos,degrees,exp,floor,log,map,max,min,radians,random,randomSeed,round,sin,sq,sqrt,tan,bitRead,bitWrite,bitSet,bitClear,bit,highByte,lowByte,analogReference,analogRead,analogWrite,attachInterrupt,detachInterrupt,delay,delayMicroseconds,digitalWrite,digitalRead,interrupts,millis,micros,noInterrupts,noTone,pinMode,pulseIn,shiftIn,shiftOut,tone,Serial,Serial1,Serial2,Serial3,begin,end,peek,read,print,println,available,flush,setTimeout,find,findUntil,parseInt,parseFloat,readBytes,readBytesUntil},
  keywordstyle={[2]\bfseries\color[rgb]{0.8,0.33,0}}}
\lstinputlisting[firstnumber=88,firstline=88,lastline=99]{../Software/Debug_test/Debug_test.ino}

\chapter{Konklusion}
Softwaren blev udviklet og opfyldte både de mål der blev sat i programmering~C, samt blev brugt i teknikfag~A-projektet til at teste Kalman-filteret.
\end{document}

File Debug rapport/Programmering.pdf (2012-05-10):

### Programmering C eksamen:

S D
af

## Mathias Dannesbo

10. maj 2012

Resumé

is journal is a walk-through of the source code of Swagway Debugger, a Windows application for debugging and tuning Kalman-lters, on balancing robots and Segway clones. It is made as a part of the Swagway project.

### 1 Indledning

Formålet med opgaven er at lave et stykke soware der kan bruges sammen med forfaerens eksamenprojekt i Teknikfag A: El. Formålet med teknikfags projektet er at bygge en Segway klon, en motoriseret selvbalancrende tohjulet transportenhed. Navnet på teknikfag A-projektet er Swagway. Under udviklingen af Swagway blev der behov for et stykke soware til at teste et lter.¹

Kort beskrivelse af Swagway funktion

For at Swagway kan holde sig lodret skal den kende vinklen den er fra lodret. Det udregner den ved at læse data fra to sensorer: et accelerometer og et gyroskop.
Et gyroskop kan måle vinkelhastigheder. Det vil sige ændringer i vinklen. Hvis denne vinkelhastighed integreres over tid nder man vinklen gyroskopet har yet sig. Problemet med at integrer gyroskopdata er, at pga. måleusikkerheder vil det målte nulpunkt drive væk fra det fysiske nulpunkt.
Et accelerometer kan måle accelerationer. Man kan med hjælp fra tangens og data fra to akser udregne den vinklen accelerometeret står i forhold til jordens tyngdekræ. Problemet med dee er at accelerometer måler alle accelerationer, ikke kun jordens tyngdekræ. Når Swagwayen fx accelerer, bremser eller køre over en sten bliver den udregnet vinkel forkert. For at komme begge problemer til livs bliver begge sensorer brugt og data fra begge to bliver samlet i et såkaldt Kalman-lter. Kalman-ltret kan tilnærmelsesvis ses som et high-pass og low-pass lter. Det taget de hurtige ændringer (high-pass) fra gyroskop-dataene og bruger accelerometer-dataene til at holde det målte og det fysiske nulpunkt ens.

Swagway Debugger

For at teste om Kalman-ltret er implementeret og tunet korrekt er det nødvendig at sammenligne de tre vinkler fra hhv. gyroskopet, accelerometeret og Kalman-ltret. En måde at gøre dee på er ved at sende disse data fra elektronikken på Swagwayen til en PC og vise dem grask. Det er her Swagway Debugger-sowaren kommer ind i billedet.
Swagway Debugger modtager data, over en seriel-port, fra en Arduino microcontroller på Swagwayen og skriver dataene på en graf. Som der står i produktbeskrivelsen:

1Websiden for hele projekter ndes på https://github.com/neic/Swagway. Derfra er der adgang til alt kildekode, rapporter og andre skrilige fremstillinger.

Mathias Dannesbo

Programmering C: Swagway Debugger
EUC Nord: HTX Frederikshavn, f11htx3.B | 10. maj 2012

Opgaven er at lave soware der kan modtage data fra en Arduino over en serielport og visualiserer det. Sowaren er til test af ltereringen af data fra et gyroskop og accelerometer. Sowaren viser bl.a. et rullende plot, samt nogle viserinstrumenter.

### 2 Udførelse

Swagway Debugger er skrevet på Microso Windows i C# som en Windows Form Application. Der er ingen eksterne aængighedder; det bruger kun Microso biblioteker:

9 | using System.IO.Ports; // Seriel -porte
10 | using System.Text.RegularExpressions; // Regular expressions
11 | using System.Globalization; // Forskel på , og .
12 | using System.Windows.Forms.DataVisualization; // Grafer

Der er fem globale variabler:

18 | string readFromUART; // Holder data læst direkte fra UART
19 | string rxStringBuffer; // Holder rest af sidste pakke
20 | List<string > rxListBuffer = new List<string >(); // Holder
pakker som liste
21
22 | int packageCount = 0;
23 | int oldPackageCount = 0;

De tre første er buffere der bliver brugt til midlertidig at gemme modtaget data i, de to sidste er tællere over antallet af pakker.

### 2.1 Indstillinger


Ved opstart af applikationen indlæses alle tilgængelige serial-porte og der sæes en standardindstilling for valget af seriel hastighed:

2

Mathias Dannesbo

Programmering C: Swagway Debugger
EUC Nord: HTX Frederikshavn, f11htx3.B | 10. maj 2012
34 | /* Kaldes ved opstart: finder seriel -porte */
35 | private void Form1_Load(object sender , EventArgs e)
36 | {
37 | LoadSerialPorts(); // Opdater listen med serialporte
38 | cbSpeed.SelectedIndex = 10; // Sætter 115200 baud som
standardindstilling
39 | }

Ved afslutning af applikationen lukkes en eventuel åben seriel-port:

41 | /* Kaldes ved afslutning: lukker seriel -porte */
42 | private void Form1_FormClosing(object sender ,
FormClosingEventArgs e)
43 | {
44 | if (serialPort.IsOpen) // Luk seriel -porten hvis den er å
ben
45 | {
46 | serialPort.Close();
47 | }
48 | }
LoadSerialPorts() kaldes ved opstart og ved tryk knappen btReload. Den føjer alle systemets serial-porte til listen, sæer den første seriel-port som standardindstilling og advare i statuslinjen hvis der ikke er fundet nogle seriel-porte:
50 | /* Finder systemets seriel -porte */
51 | private void LoadSerialPorts()
52 | {
53 | cbComPort.Items.Clear(); // Ryd listen
54
55 | foreach (string s in SerialPort.GetPortNames()) // For
alle serielporte i systemet
56 | {
57 | cbComPort.Items.Add(s); // Føj til listen
58 | }
59
60 | if (cbComPort.Items.Count > 0) // Hvis der er fundet
seriel -porte
61 | {
62 | cbComPort.SelectedIndex = 0; // Sætter den første
seriel -port som standardinstilling
63 | }
64 | else
65 | {
66 | lbConnectionStatus.Text = "No COM-ports found"; //
Ellers advarer i statuslinjen
67 | }
68 | }
Eventhandleren for btConnect både forbinder og aryder til en seriel-port. Hvis der er arud nder den hvilken seriel-port og hastighed der er valgt, forbinder og opdaterer statuslinjen og dens egen tekst til “Disconnect”. Hvis der er opreet forbindelse aryder den og ligeledes opdaterer statuslinjen og dens egen tekst til “Connect”:
76 | /* Forbind og afbryd til serielporten */
77 | private void btConnect_Click(object sender , EventArgs e)

3

Mathias Dannesbo

Programmering C: Swagway Debugger
EUC Nord: HTX Frederikshavn, f11htx3.B | 10. maj 2012
78 | {
79 | if (btConnect.Text == "Connect") // Hvis der skal
forbindes
80 | {
81 | if (!serialPort.IsOpen) // Hvis der ikke er forbundet
82 | {
83 | serialPort.PortName = cbComPort.SelectedItem.
ToString(); // Find navnet på porten
84 | serialPort.BaudRate = int.Parse(cbSpeed.
SelectedItem.ToString()); // Find hastigheden
85 | serialPort.Open(); // Forbind
86 | }
87
88 | if (serialPort.IsOpen) // Hvis forbindelsen lykkedes
89 | {
90 | lbConnectionStatus.Text = "Connected to: " +
serialPort.PortName; // Skriv i statuslinjen
91 | btConnect.Text = "Disconnect"; // Lav knappen om
til afbryd
92 | }
93 | }
94 | else // Hvis der skal afbrydes
95 | {
96 | if (serialPort.IsOpen) // Hvis der er forbindelse
97 | {
98 | serialPort.Close(); // Afbryd
99 | }
100
101 | lbConnectionStatus.Text = "Disconnected"; // Skriv i
status linjen
102 | btConnect.Text = "Connect"; // Lav knappen om til
forbind
103 | }
104 | }
NumericUpDown-tælleren, udPackages, bestemmer hvor meget data der skal vises på grafen. Når værdien i tælleren ændres ændre den dynamisk skala. Endeligt opdaterer den grafens X-akses maksimalværdi:
106 | /* Længden af X-aksen på grafen */
107 | private void udPackages_ValueChanged(object sender ,
EventArgs e) // Bliver kaldt hver gang tallet ændres
108 | {
109 | if (udPackages.Value <= 1000) // Hvis værdien er under
eller ligemed 1000 skal den ændres med 100
110 | {
111 | udPackages.Increment = 100;
112 | }
113
114 | if (udPackages.Value > 1000) // Hvis værdien er over 1000
skal den ændres med 1000
115 | {
116 | udPackages.Increment = 1000;
117 | }
118

4

Mathias Dannesbo

Programmering C: Swagway Debugger
EUC Nord: HTX Frederikshavn, f11htx3.B | 10. maj 2012
119 | if (udPackages.Value == 1100) // Er værdien 1100 skal den
være 2000
120 | {
121 | udPackages.Value = 2000;
122 | }
123
124 | chart1.ChartAreas.First().AxisX.Maximum = (double)
udPackages.Value; // Set X-aksens maksimum værdi
125 | }

### 2.2 Seriel modtagelse og monitor


Når der, eer der er forbundet til en seriel-port, ankommer data lægges det i bufferen readFromUART og ReadToMonitor kaldes:

131 | /* Læs inkommende data til buffer og kald ReadToMonitor()
| */
132 | private void serialPort_DataReceived(object sender ,
| SerialDataReceivedEventArgs e)
133 | {
134 | readFromUART = serialPort.ReadExisting();
135 | this.BeginInvoke(new EventHandler(ReadToMonitor));
136 | }
ReadToMonitor Skriver den modtaget data, readFromUART, direkte til monitoren uden at behandle den. Den undesøger om der er meget data i monitoren og sleer en smugle af det ældste hvis det er tilfældet. Til slut kalder den CleanData().
138 | /* Skriver rå data til monitor , ryder op i monitor og
| kalder CleanData()*/
139 | private void ReadToMonitor(object sender , EventArgs e)
140 | {
141 | tbMonitor.AppendText(readFromUART); // Tilføjer til
| monitor

5

Mathias Dannesbo

Programmering C: Swagway Debugger
EUC Nord: HTX Frederikshavn, f11htx3.B | 10. maj 2012

142
143 | if (tbMonitor.TextLength > 50000) // Hvis der mere end ca
. 2000 pakker i monitor
144 | {
145 | tbMonitor.Lines = tbMonitor.Lines.Skip(20).ToArray();
// Slet 20 linjer
146 | }
147
148 | CleanData(readFromUART); // Kalder CleanData()
149 | }

Datapakkerne fra Swagwayen er af formen < ⟨gyro⟩, ⟨acc⟩, ⟨kalm⟩, ⟨tid⟩ >

Hvor
⟨gyro⟩ er vinklen målt med gyroskopet med to decimaler og eventuelt negativt fortegn,
⟨acc⟩ er vinklen målt med accelerometeret med to decimaler og eventuelt negativt fortegn, ⟨gyro⟩ er vinklen udregnet af Kalman-ltret med to decimaler og eventuelt negativt fortegn og ⟨tid⟩ er tiden i µSS siden sidste pakke blev sendt.

CleanData() tager den rå modtaget data, readFromUART, og tilføjer det til en ny buffer, rxStringBuffer. Den indeholder allerede en rest data fra sidste gang. Denne buffer bliver spliet og hver pakke bliver indsat i listen rxListBuffer. Den sidste, ikke fuldstændige, pakke bliver lagt tilbage i rxStringBuffer og er klar til at bliver parret sammen ved næste kald af CleanData():

151 | /* Tager rå data , rengør det og sender det til graf */
152 | private void CleanData(string input)
153 | {
154 | rxStringBuffer += input; // Tilføjer nyt rå data fra UART
155 | rxListBuffer = rxStringBuffer.Split('<').ToList(); //
Splitter ved hver begyndelse af ny pakke '<'
156 | rxStringBuffer = rxListBuffer[rxListBuffer.Count() - 1];
// Ligger den sidste , ikke fuldstændige , pakke tilbage i buffer
157 | rxListBuffer.Remove(rxListBuffer.Last()); // Sletter den
ikke fuldstendige pakke fra listen
Pakkerne i rxListBuffer bliver renset for alt der står eer “>” og bliver undersøgt om de passer ind i formen for en pakke af en regular expression. Hvis den gør dee bliver pakken spliet til et array af strings for dereer at bliver parset til et array af floats. Dee array bliver givet vidre til til funktionen plotPackage():
159 | /* For alle nye pakker */
160 | for (int i = 0; i < rxListBuffer.Count(); i++)
161 | {
162 | /* Slet alt efter slutningen af pakken '>' */
163 | int j = rxListBuffer[i].IndexOf('>'); // Finder
indexet af '>'
164 | if (j > 0)
165 | {
166 | rxListBuffer[i] = rxListBuffer[i].Substring(0, j)
; // Klipper fra begyndelsen til indexet af '>'
167 | }
168 | /* End : Selt efter slutning*/

6

Mathias Dannesbo

Programmering C: Swagway Debugger
EUC Nord: HTX Frederikshavn, f11htx3.B | 10. maj 2012

169
170 | /* God pakke? Så plot den */
171 | if (Regex.Match(rxListBuffer[i], @"^((-?\d{1,3}[.]\d\
d,){3,3}\d{4,})$").Success) //Pakken undersøges om den passer ind.
172 | {
173 | string[] stringPackage = rxListBuffer[i].Split
(',').ToArray(); // Pakken splittes til et string -array
174 | float[] floatPackage = new float[4];
175
176 | for (int k = 0; k < stringPackage.Length; k++) //
String -arrayet parses til et float -array
177 | {
178 | float.TryParse(stringPackage[k], NumberStyles
.Float , CultureInfo.InvariantCulture , out floatPackage[k]);
179 | /* TryParse prøver at parse , hvis det ikke er
muligt bliver pakken droppet.
180 | * CultureInfo er nødvendigt for at kunne
bruge "." som decimaltegn */
181 | }
182
183 | packageCount++;
184 | plotPackage(floatPackage); // Send float -arrayet
til grafen
185 | }
186 | /* End : God pakke */
187 | }
188 | /* End : For alle nye */
189 | }

Applikationen kan også sende data. Det er undladt af journalen. Se hvordan virker på linje 195–218 af Form1.cs.

### 2.3 Graf

Når en ny pakke er blevet renset, bliver hver del af den tilføjet grafen i forskellige serier. Tiden bliver ignoreret. Der bliver så undersøgt om der er ere pakker end grænseværdien. Hvis der er det, bliver de ernet fra grafen:

224 | /* Tilføjer pakke til graf og rydder op */
225 | private void plotPackage(float[] package)
226 | {
227 | for (int i = 0; i < package.Length -1; i++) // Plot alle
punkterne i pakken til hver sin serie
228 | {
229 | chart1.Series[i].Points.AddY(package[i]);
230 | }
231
232 | if (packageCount > udPackages.Value) // Slet alle pakker
over grænseværdi
233 | {
234 | for (int i = 0; i < package.Length -1; i++)

7

Mathias Dannesbo

Programmering C: Swagway Debugger
EUC Nord: HTX Frederikshavn, f11htx3.B | 10. maj 2012


235 | {
236 | chart1.Series[i].Points.RemoveAt(0);
237 | }
238 | }
239 | }

### 2.4 Statuslinje

En timer kalder hvert sekund eventhandleren timerSample_Tick undersøger hvor mange pakker der er tilføjet det sidste sekund. Den skriver antallet til statuslinjen og opdaterer en statusbjælke:

245 | /* Udregn antal pakker per sekund */
246 | private void timerSample_Tick(object sender , EventArgs e)
| // Kaldes hvert sekund
247 | {
248 | int diff = packageCount - oldPackageCount; // Forskellen
| i antallet pakker siden sidste sekund
249 | lbSamplesPerSec.Text = diff.ToString() + " Samples/sec";
| // Skriv det på status linjen
250
251 | if (diff>pbSamplesPerSec.Maximum) // Hvis forskellen er
| større en maksimum af statusbjælken
252 | {
253 | pbSamplesPerSec.Maximum = diff; // Forstør makimum
254 | }
255
256 | pbSamplesPerSec.Value = diff; // Set statusbjælken til
| antallet af pakker per sekund
257 | oldPackageCount = packageCount;
258 | }

8

Mathias Dannesbo

Programmering C: Swagway Debugger
EUC Nord: HTX Frederikshavn, f11htx3.B | 10. maj 2012

### 3 Debug_test.ino

Swagway projektet med gyroskopet og accelerometeret er aeveret, så for at teste Swagway Debugger er der lavet et lille test program til en Arduino. Til Arduinoen er der tilkoblet to potentiometerere til at simulere data fra gyroskop og accelerometer. Den del af sowaren som har interesse er den som sender pakken med data:

88 | void sendToGraph()
89 | {
90 | Serial.print("<");
91 | Serial.print(gyroAngle); //0
92 | Serial.print(",");
93 | Serial.print(accAngle); //1
94 | Serial.print(",");
95 | Serial.print(estAngle); //2
96 | Serial.print(",");
97 | Serial.print(micros()-sinceLastSend); //3
98 | Serial.println(">");
99 | }

### 4 Konklusion

Sowaren blev udviklet og opfyldte både de mål der blev sat i programmering C, samt blev brugt i teknikfag A-projektet til at teste Kalman-lteret.

9

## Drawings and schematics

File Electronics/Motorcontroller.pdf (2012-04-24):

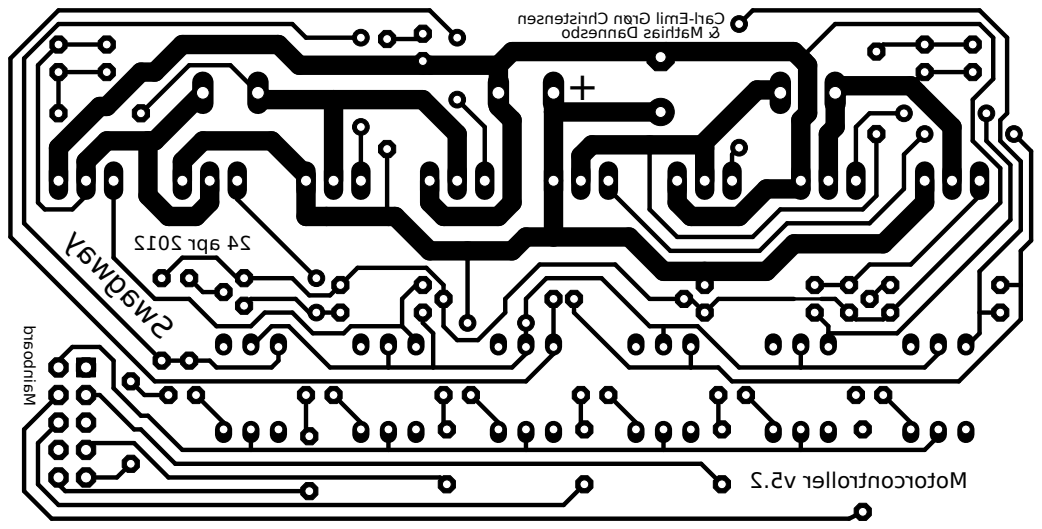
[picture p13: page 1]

nesnetsi r hC nør Gli mE-l r aC

2. 5vr ell ort nocr ot o M

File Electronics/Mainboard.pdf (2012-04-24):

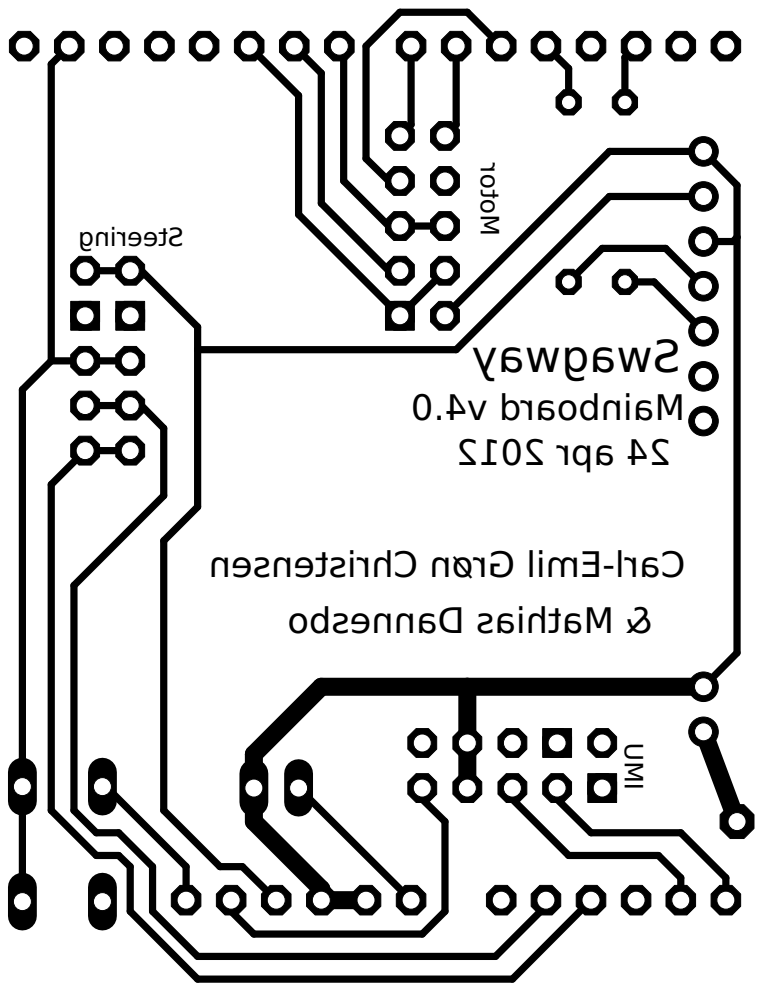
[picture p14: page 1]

nesnet si r hC nør Gli mE-l r aC

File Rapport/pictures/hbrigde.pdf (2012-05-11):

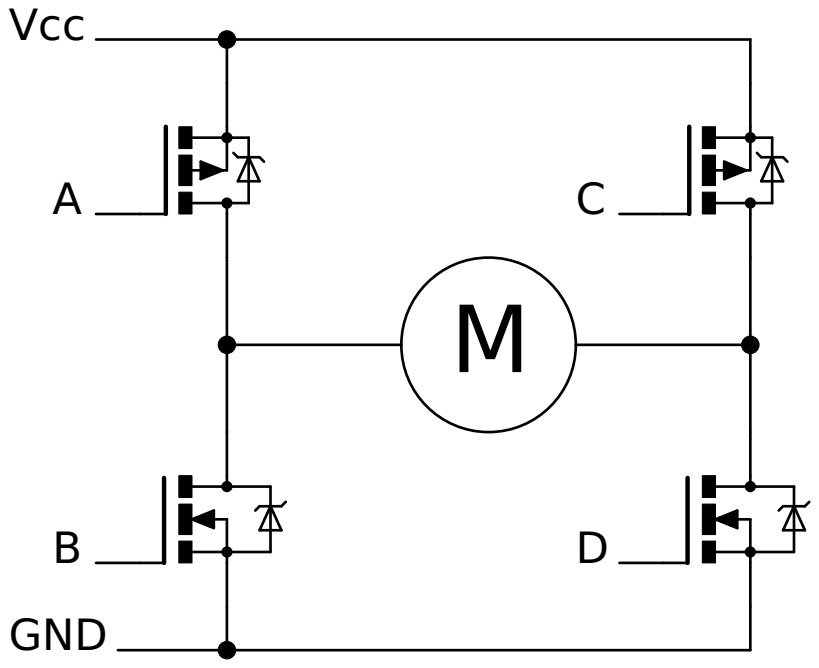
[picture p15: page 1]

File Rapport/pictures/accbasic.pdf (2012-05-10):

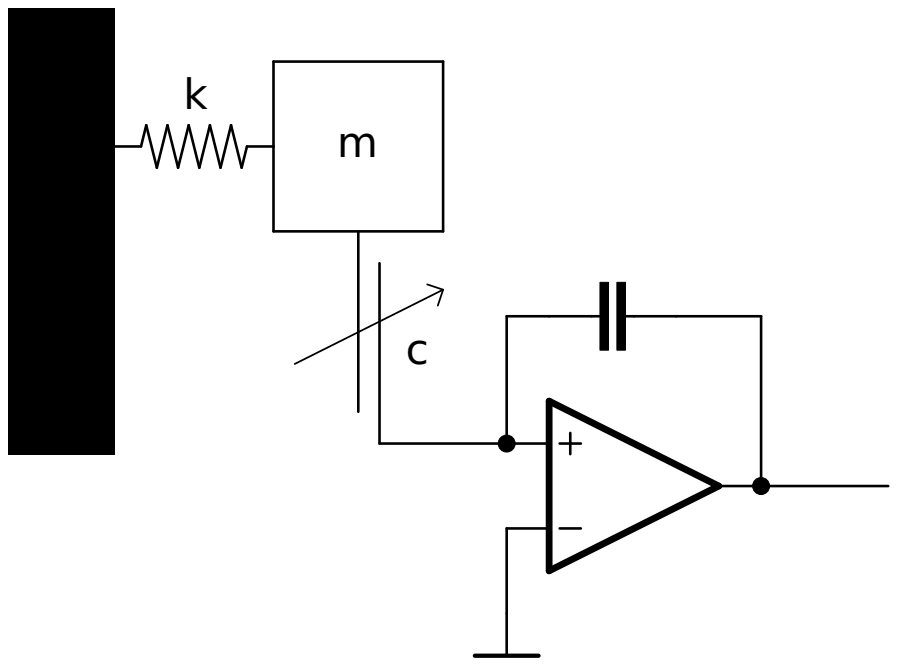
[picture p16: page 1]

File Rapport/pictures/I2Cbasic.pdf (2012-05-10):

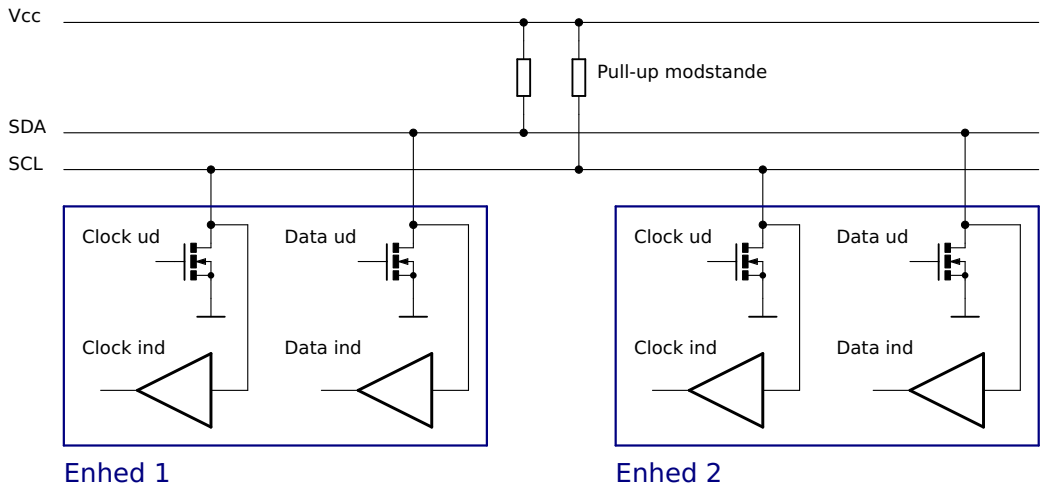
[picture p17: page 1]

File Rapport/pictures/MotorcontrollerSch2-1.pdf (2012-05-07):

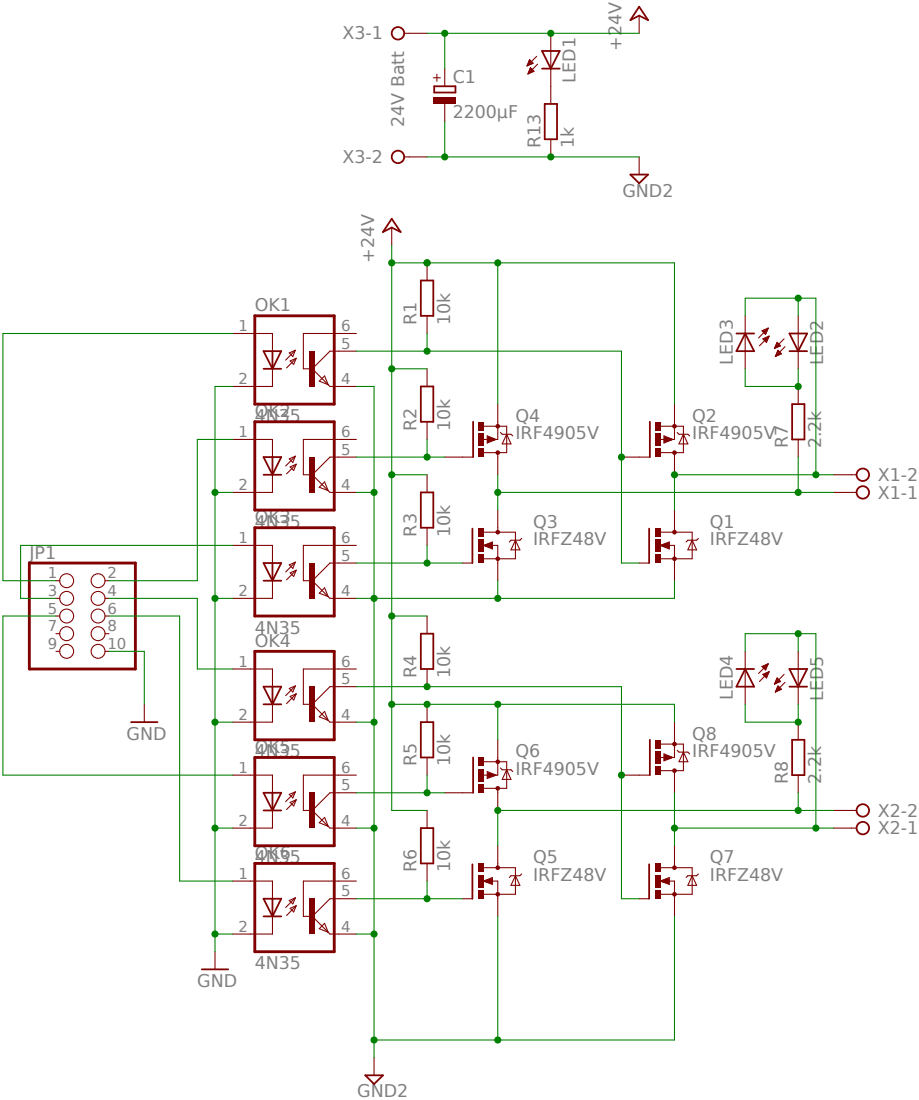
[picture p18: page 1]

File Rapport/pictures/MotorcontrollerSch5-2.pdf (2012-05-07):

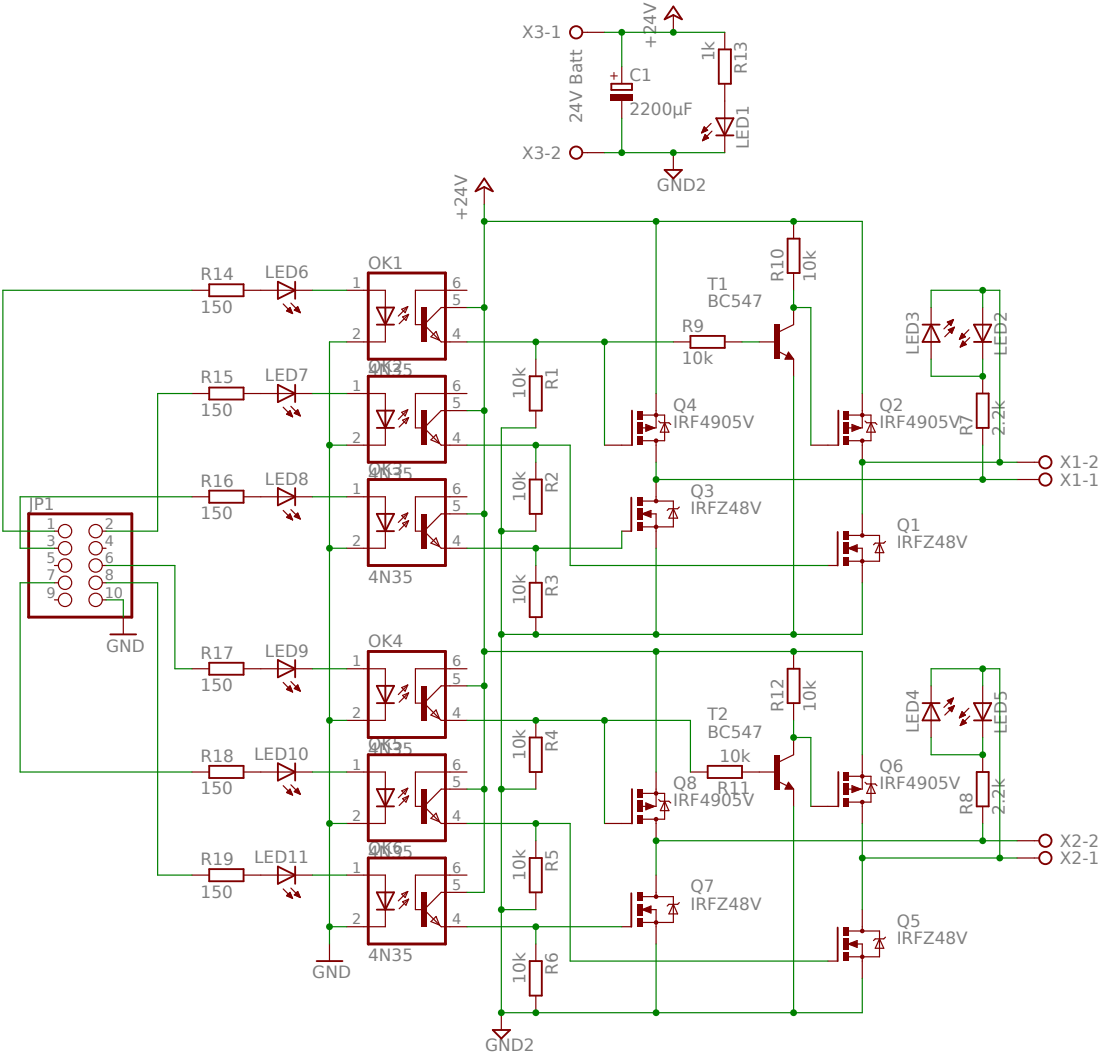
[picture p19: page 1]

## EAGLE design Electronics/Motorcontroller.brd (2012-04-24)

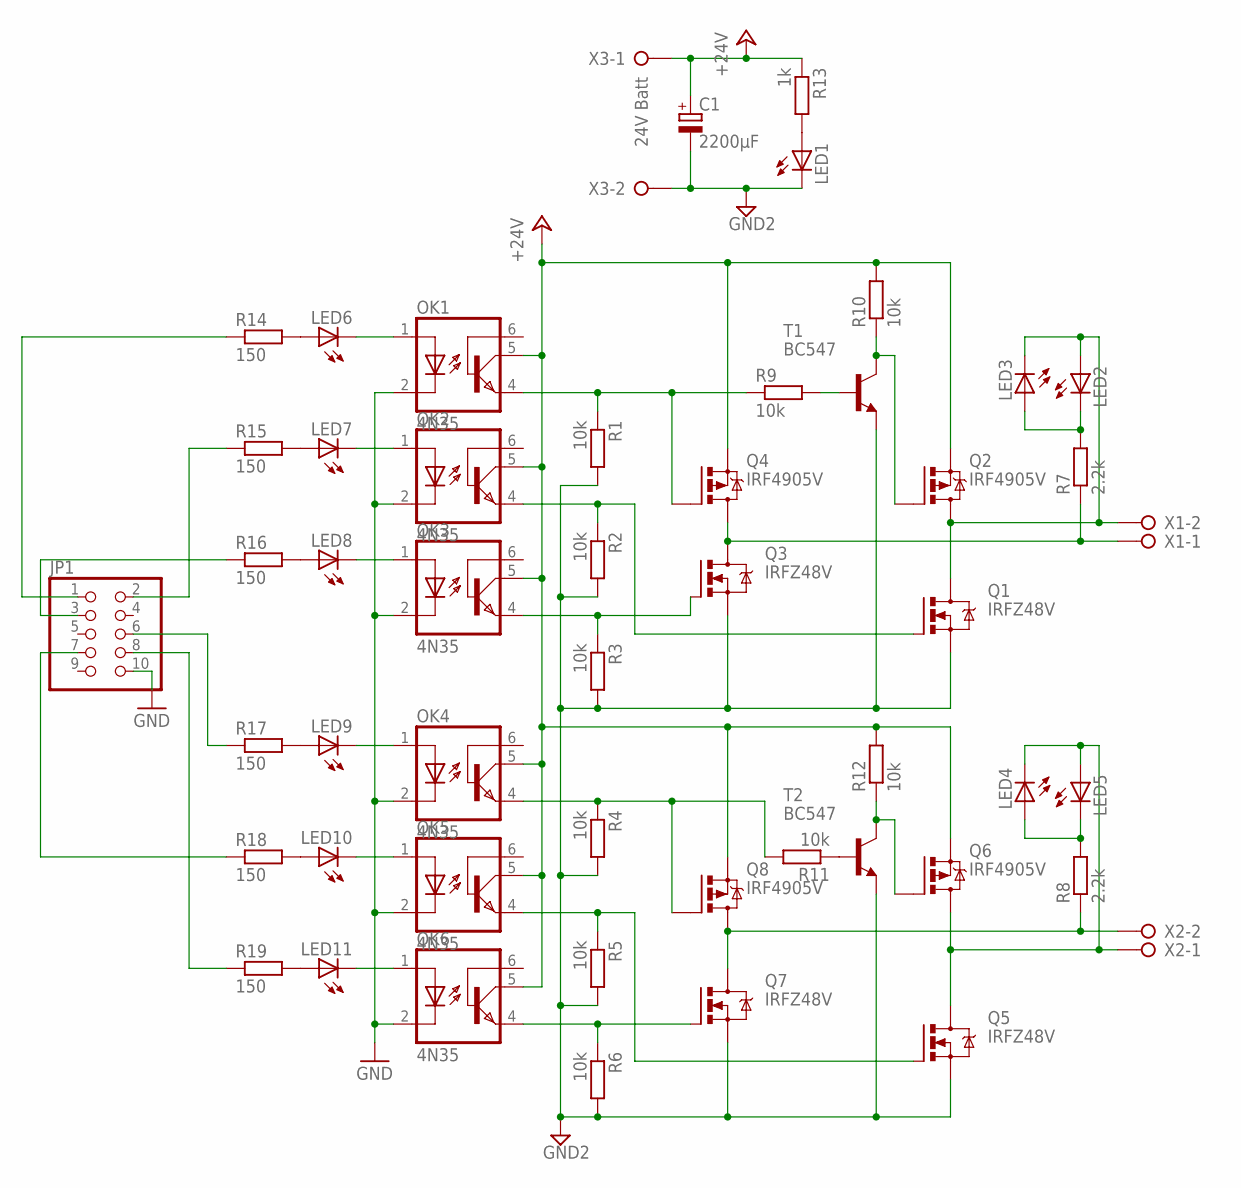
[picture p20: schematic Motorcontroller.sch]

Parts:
C1: 2200µF; E5-13
JP1: PINHD-2X5; 2X05
LED1, LED2, LED3, LED4, LED5, LED6, LED7, LED8, LED9, LED10, LED11: LED3MM
OK1, OK2, OK3, OK4, OK5, OK6: 4N35; DIL06
Q1, Q3, Q5, Q7: IRFZ48V; TO220BV
Q2, Q4, Q6, Q8: IRF4905V; TO220BV
R1, R2, R9, R10: 10k; 0207/7
R3, R4, R5, R6, R11, R12: 10k; 0207/10
R7, R8: 2.2k; 0207/7
R13: 1k; 0207/10
R14, R19: 150; 0207/7
R15, R16, R17, R18: 150; 0207/5V
T1, T2: BC547; TO92
X1, X2: W237-02P; W237-132
X3: 24V Batt; W237-132

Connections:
+24V: C1.+, OK1.5 (COL), OK2.5 (COL), OK3.5 (COL), OK4.5 (COL), OK5.5 (COL), OK6.5 (COL), Q2.S, Q4.S, Q6.S, Q8.S, R10.2, R12.2, R13.1, X3.1
GND: JP1.10, OK1.2 (C), OK2.2 (C), OK3.2 (C), OK4.2 (C), OK5.2 (C), OK6.2 (C)
GND2: C1.-, LED1.K (C), Q1.S, Q3.S, Q5.S, Q7.S, R1.2, R2.2, R3.2, R4.2, R5.2, R6.2, T1.1 (E), T2.1 (E), X3.2
unnamed: LED4.K (C), LED5.A, Q5.D, Q6.D, X2.1
unnamed: Q3.D, Q4.D, R7.1, X1.1
unnamed: JP1.1, R14.1
unnamed: LED2.A, LED3.K (C), Q1.D, Q2.D, X1.2
unnamed: JP1.2, R15.1
unnamed: LED1.A, R13.2
unnamed: JP1.3, R16.1
unnamed: JP1.6, R17.1
unnamed: OK2.4 (EMI), Q1.G, R2.1
unnamed: JP1.7, R18.1
unnamed: JP1.8, R19.1
unnamed: OK1.4 (EMI), Q4.G, R1.1, R9.1
unnamed: OK3.4 (EMI), Q3.G, R3.1
unnamed: R9.2, T1.2 (B)
unnamed: Q2.G, R10.1, T1.3 (C)
unnamed: OK4.4 (EMI), Q8.G, R4.1, R11.2
unnamed: LED10.A, R18.2
unnamed: R11.1, T2.2 (B)
unnamed: Q6.G, R12.1, T2.3 (C)
unnamed: LED6.A, R14.2
unnamed: OK5.4 (EMI), Q5.G, R5.1
unnamed: OK6.4 (EMI), Q7.G, R6.1
unnamed: LED2.K (C), LED3.A, R7.2
unnamed: LED4.A, LED5.K (C), R8.2
unnamed: Q7.D, Q8.D, R8.1, X2.2
unnamed: LED7.A, R15.2
unnamed: LED8.A, R16.2
unnamed: LED9.A, R17.2
unnamed: LED11.A, R19.2
unnamed: LED6.K (C), OK1.1 (A)
unnamed: LED7.K (C), OK2.1 (A)
unnamed: LED8.K (C), OK3.1 (A)
unnamed: LED9.K (C), OK4.1 (A)
unnamed: LED10.K (C), OK5.1 (A)
unnamed: LED11.K (C), OK6.1 (A)

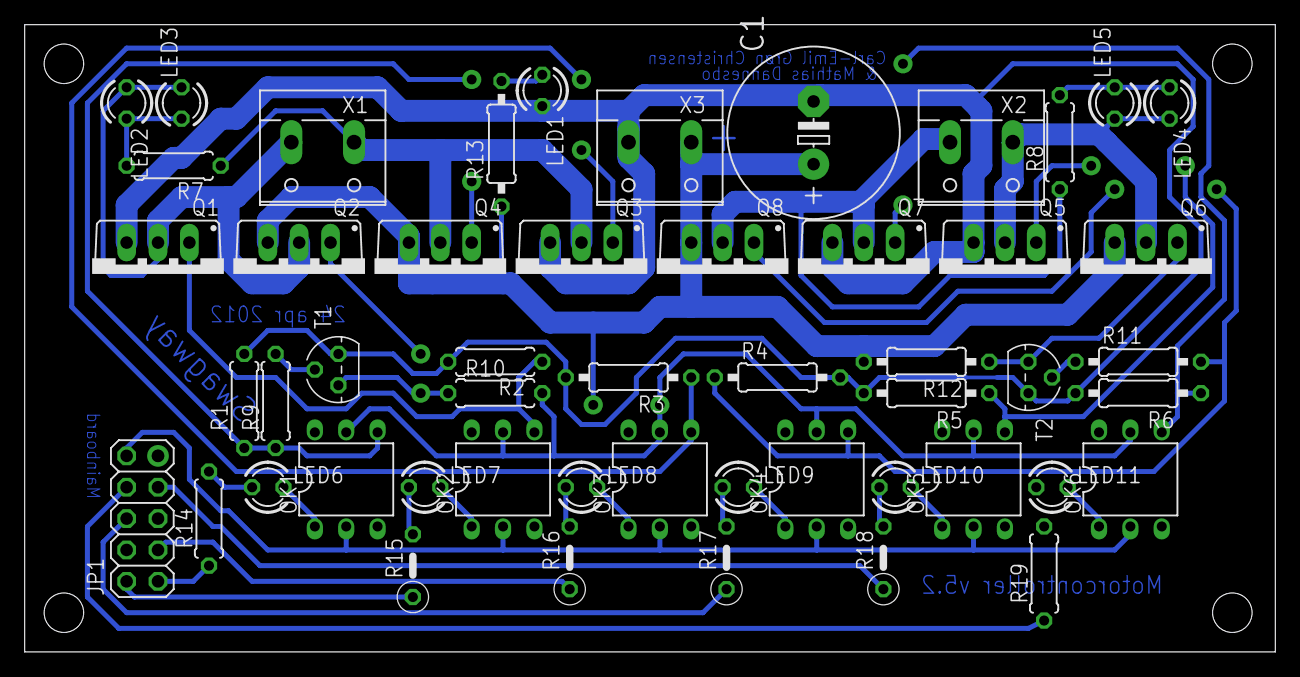
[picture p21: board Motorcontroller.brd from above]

Board: 2 copper layers, 101.3 x 50.8 mm, 51 parts (0 on the bottom side), 38 nets.

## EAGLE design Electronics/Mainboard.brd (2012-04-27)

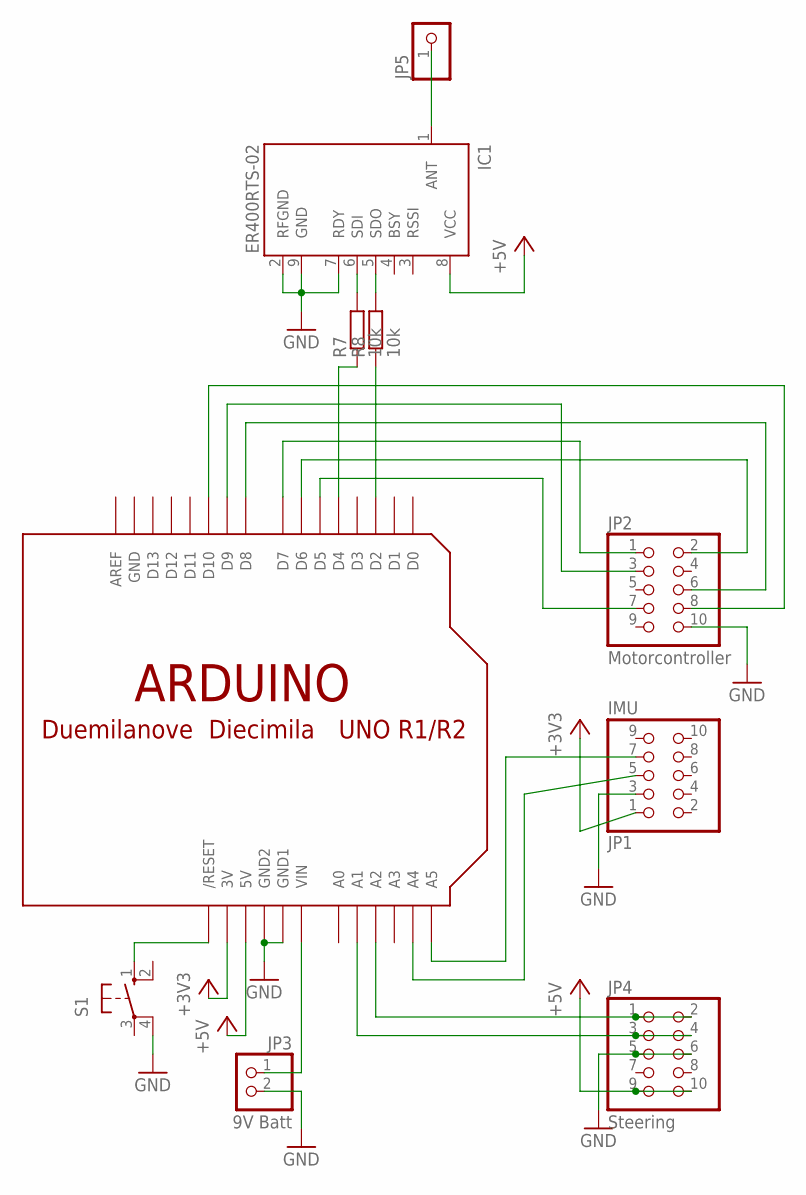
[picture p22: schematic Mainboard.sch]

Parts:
IC1: ER400RTS-02; SIL9
JP1: IMU; 2X05
JP2: Motorcontroller; 2X05
JP3: 9V Batt; 1X02
JP4: Steering; 2X05
JP5: PINHD-1X1; 1X01
R7, R8: 10k; 0207/10
S1: 10-XX; B3F-10XX
U$1: ARDUINOUNO; ARDUINO

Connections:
+3V3: JP1.1, U$1.3V
+5V: IC1.8 (VCC), JP4.9, JP4.10, U$1.5V
GND: IC1.2 (RFGND), IC1.7 (RDY), IC1.9 (GND), JP1.3, JP2.10, JP3.2, JP4.5, JP4.6, S1.4 (P1), U$1.GND, U$1.GND1, U$1.GND2
unnamed: JP2.1, U$1.D7
unnamed: JP2.2, U$1.D6
unnamed: JP2.6, U$1.D8
unnamed: JP2.8, U$1.D10
unnamed: JP2.3, U$1.D9
unnamed: R8.1, U$1.D2
unnamed: R7.1, U$1.D4
unnamed: JP4.3, JP4.4, U$1.A1
unnamed: JP4.1, JP4.2, U$1.A2
unnamed: S1.1 (S), U$1.RESET (/RESET)
unnamed: JP2.7, U$1.D5
unnamed: IC1.5 (SDO), R8.2
unnamed: IC1.6 (SDI), R7.2
unnamed: IC1.1 (ANT), JP5.1
unnamed: JP1.7, U$1.A5
unnamed: JP3.1, U$1.VIN
unnamed: JP1.5, U$1.A4

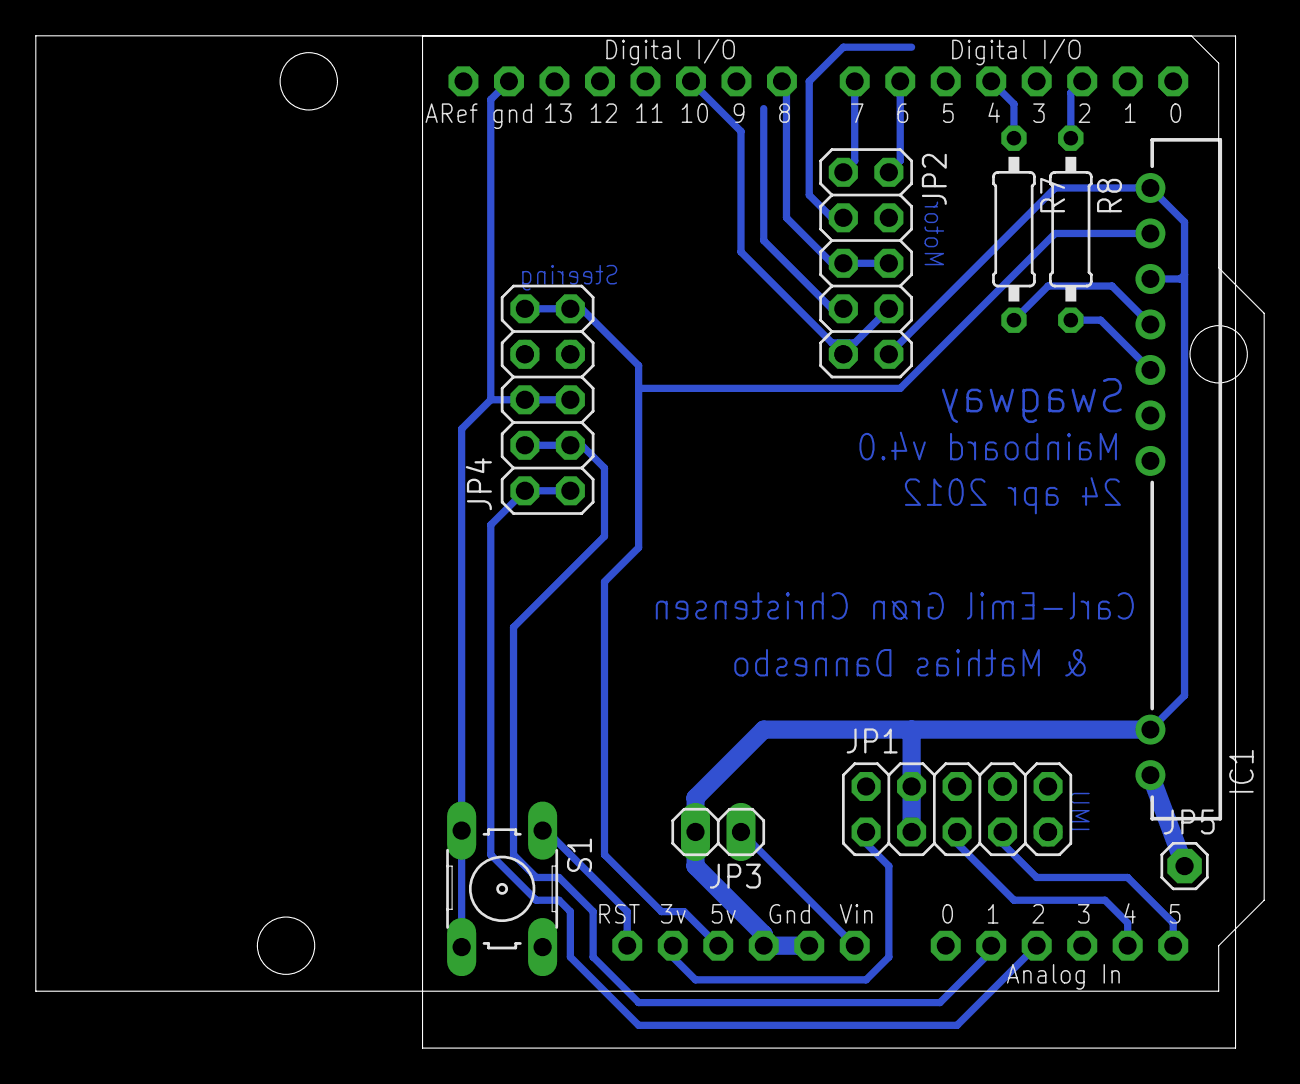
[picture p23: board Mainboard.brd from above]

Board: 2 copper layers, 68.6 x 56.5 mm, 10 parts (0 on the bottom side), 20 nets.

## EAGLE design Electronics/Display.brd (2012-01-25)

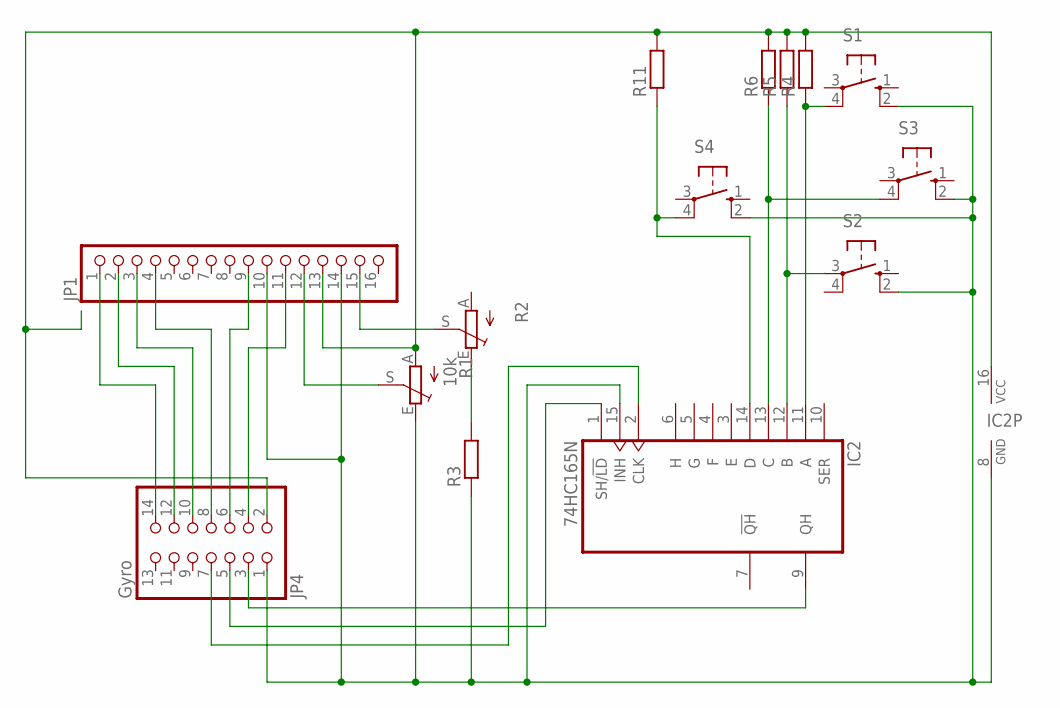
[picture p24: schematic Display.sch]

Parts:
IC2: 74HC165N; DIL16
JP1: PINHD-1X16; 1X16
JP4: Gyro; 2X07
R1: 10k; CA9H
R2: TRIM_EU-CA9H; CA9H
R3, R4, R5, R6, R11: R-EU_0207/10; 0207/10
S1, S2, S3, S4: 10-XX; B3F-10XX

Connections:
unnamed: JP1.15, R2.S
unnamed: IC2.8 (GND), IC2.15 (INH), JP1.10, JP1.14, JP4.1, R1.E, R3.1, S1.2 (S1), S2.2 (S1), S3.2 (S1), S4.2 (S1)
unnamed: JP1.13, JP4.2, R1.A, R4.2, R5.2, R6.2, R11.2
unnamed: R2.E, R3.2
unnamed: JP1.11, JP4.4
unnamed: IC2.1 (SH/!LD), JP4.5
unnamed: JP1.12, R1.S
unnamed: IC2.9 (QH), JP4.3
unnamed: IC2.2 (CLK), JP4.7
unnamed: JP1.9, JP4.6
unnamed: JP1.4, JP4.8
unnamed: JP1.3, JP4.10
unnamed: JP1.2, JP4.12
unnamed: JP1.1, JP4.14
unnamed: IC2.11 (A), R4.1, S1.4 (P1)
unnamed: IC2.12 (B), R5.1, S2.3
unnamed: IC2.13 (C), R6.1, S3.4 (P1)
unnamed: IC2.14 (D), R11.1, S4.4 (P1)
VCC: IC2.16 (VCC)

Board: 2 copper layers, 14 parts (0 on the bottom side), 18 nets, no tracks yet.

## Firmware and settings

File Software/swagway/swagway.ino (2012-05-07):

/*************************************************/
/* swagway.ino -- Swagway onboard software       */
/*                                               */
/* Author: Mathias Dannesbo <neic@neic.dk> and   */
/*         Carl-Emil Grøn Christensen            */
/* Time-stamp: <2012-05-07 18:07:19 (neic)>      */
/* Part of the Swagway project                   */
/* https://github.com/neic/Swagway               */
/*                                               */
/*************************************************/

#include <Wire.h>
#include <math.h>
#include "ITG3200.h"
#include "ADXL345.h"

// IMU
ADXL345 acc = ADXL345();
float accSampleRate;
ITG3200 gyro = ITG3200();
float gyroSampleRate;

// General
int xa, ya, za;
float xg, yg, zg;

unsigned long sinceLastSend;

bool newAccData, newGyroData;

double accAngle, gyroAngle, estAngle;

// Kalman filter
const float Q_angle = 0.001; // Process noise covariance for the accelerometer - Sw
const float Q_gyro = 0.003; // Process noise covariance for the gyro - Sw
const float R_angle = 0.03; // Measurement noise covariance - Sv

double angle = 0; // It starts at 0 degrees
double bias = 0;
double P_00 = 0, P_01 = 0, P_10 = 0, P_11 = 0;
double dt, y, S;
double K_0, K_1;

// Motor

const int directionPinLeft = 7; //HIGH when forward
const int forwardPinLeft = 9;
const int backwardPinLeft = 6;

const int directionPinRight = 8; //HIGH when forward
const int forwardPinRight = 10;
const int backwardPinRight = 5;

// PID

const int targetAngle = 0;
const float Ex = 2.6; //Exponential value
const float Kp = 2; //Proportional value

void setup() 
{
  Serial.begin(115200);
  Wire.begin();

  //Init the acc
  acc.init(ADXL345_ADDR_SD0_LOW);
  acc.setFullRes(true);
  acc.setRange(3);
  acc.setVoltage(3.3);
  acc.setOutputRate(10); //25Hz*2^(10-8)=100Hz. See table 7 in ADXL345 datasheet

  //Calculate the accSampleRate
  accSampleRate = 25*pow(2,(acc.getOutputRate()-8)); //See table 7 in ADXL345 datasheet

  //Init the gyro
  gyro.init(ITG3200_ADDR_AD0_LOW);
  gyro.setSampleRateDiv(79); //Set the sample rate to 8000Hz/(79+1)=100Hz

  //Calculate the gyroSampleRate
  if (gyro.getFilterBW() == BW256_SR8)
  {
    gyroSampleRate = 8000 / (gyro.getSampleRateDiv()+1);
  }
  else
  {
    gyroSampleRate = 1000 / (gyro.getSampleRateDiv()+1);
  }

  pinMode(directionPinLeft, OUTPUT);
  pinMode(forwardPinLeft, OUTPUT);
  pinMode(backwardPinLeft, OUTPUT);
  pinMode(directionPinRight, OUTPUT);
  pinMode(forwardPinRight, OUTPUT);
  pinMode(backwardPinRight, OUTPUT);
  //Calibration
  gyro.zeroCalibrate(250,2);

  //Dump settings
  dumpIMUsettings();
}

void loop() 
{
  if (acc.isRawDataReady())
  {
    acc.readAccRaw(&xa,&ya,&za);
    accAngle = atan2(xa,ya)*180/3.1415; // calcutalte the X-Y-angle
    newAccData = true;
  }

  if (gyro.isRawDataReady())
  {
    gyro.readGyro(&xg,&yg,&zg);
    gyroAngle += zg/gyroSampleRate;
    newGyroData = true;
  }

  if (newAccData && newGyroData)
  {
    estAngle = kalman(accAngle, zg, micros()-sinceLastSend);
    //      sendToGraph();
    newAccData = newGyroData = false;
    float pwm = pid(estAngle);
    motorControl(pwm,pwm);
    Serial.print(estAngle);
    Serial.println(pwm);

    sinceLastSend = micros();
  }
}

  double kalman(double newAngle, double newRate, double dtime) {
    // KasBot V2 - Kalman filter module - http://www.arduino.cc/cgi-bin/yabb2/YaBB.pl?num=1284738418 - http://www.x-firm.com/?page_id=145
    // with slightly modifications by Kristian Lauszus
    // See http://academic.csuohio.edu/simond/courses/eec644/kalman.pdf and http://www.cs.unc.edu/~welch/media/pdf/kalman_intro.pdf for more information
      dt = dtime / 1000000; // Convert from microseconds to seconds

    // Discrete Kalman filter time update equations - Time Update ("Predict")
    // Update xhat - Project the state ahead
    angle += dt * (newRate - bias);

    // Update estimation error covariance - Project the error covariance ahead
    P_00 += -dt * (P_10 + P_01) + Q_angle * dt;
    P_01 += -dt * P_11;
    P_10 += -dt * P_11;
    P_11 += +Q_gyro * dt;

    // Discrete Kalman filter measurement update equations - Measurement Update ("Correct")
    // Calculate Kalman gain - Compute the Kalman gain
    S = P_00 + R_angle;
    K_0 = P_00 / S;
    K_1 = P_10 / S;

    // Calculate angle and resting rate - Update estimate with measurement zk
    y = newAngle - angle;
    angle += K_0 * y;
    bias += K_1 * y;

    // Calculate estimation error covariance - Update the error covariance
    P_00 -= K_0 * P_00;
    P_01 -= K_0 * P_01;
    P_10 -= K_1 * P_00;
    P_11 -= K_1 * P_01;

    return angle;
  }

float pid(float input)
{
  float output;
  if (input>0)
  {
   output = pow(input,Ex) + Kp*input;
  }
  else
  {
    output = -pow(-input,Ex) + Kp*input;
  }
  return constrain(output, -255, 255);
}

void motorControl(int left, int right)
{
  if (left < 0)
  {
    digitalWrite(directionPinLeft, HIGH);
    digitalWrite(backwardPinLeft, LOW);
    analogWrite(forwardPinLeft, -left);
  }
  else
  {
    digitalWrite(directionPinLeft, LOW);
    digitalWrite(forwardPinLeft, LOW);
    analogWrite(backwardPinLeft, left);
  }
  if (right < 0)
  {
    digitalWrite(directionPinRight, HIGH);
    digitalWrite(backwardPinRight, LOW);
    analogWrite(forwardPinRight, -right);
  }
  else
  {
    digitalWrite(directionPinRight, LOW);
    digitalWrite(forwardPinRight, LOW);
    analogWrite(backwardPinRight, right);
  }
}
/* Serial communication */

void sendToGraph()
{
  Serial.print("<");
  Serial.print(gyroAngle); //0
  Serial.print(",");
  Serial.print(accAngle); //1
  Serial.print(",");
  Serial.print(estAngle); //2
  Serial.print(",");
  Serial.print(micros()-sinceLastSend); //3
  Serial.println(">");
}

void dumpIMUsettings()
{
  Serial.println();
  Serial.println("========================================");
  Serial.println("==============IMU Settings==============");
  Serial.println();
  Serial.println("              ---Gyro---                ");
  Serial.print("Sample rate                  (Hz) = ");
  Serial.println(gyroSampleRate,0);
  Serial.println();
  Serial.println("               ---Acc---                ");
  Serial.print("Sample rate                  (Hz) = ");
  Serial.println(accSampleRate,0);
  Serial.print("Full resolution                   = ");
  Serial.println(acc.getFullRes());
  Serial.print("Range                         (g) = ");
  Serial.println(pow(2,(1+acc.getRange())),0);
  Serial.print("Scale factor X            (LBS/g) = ");
  Serial.println(acc.scaleFactor[0],0);
  Serial.print("Scale factor Y            (LBS/g) = ");
  Serial.println(acc.scaleFactor[1],0);
  Serial.print("Scale factor Z            (LBS/g) = ");
  Serial.println(acc.scaleFactor[2],0);
  Serial.println();
  Serial.println("============end IMU Settings============");
  Serial.println("========================================");
  Serial.println();
}

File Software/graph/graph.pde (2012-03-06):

/* This will only plot one data point per frame and will dispose all data in between two frames. */

import processing.serial.*;
import org.gwoptics.graphics.graph2D.Graph2D;
import org.gwoptics.graphics.graph2D.traces.ILine2DEquation;
import org.gwoptics.graphics.graph2D.traces.RollingLine2DTrace;
 
Serial myPort;
float gyro = 0;
float acc = 0;
float est = 0;
float t1 = 0;
float t2 = 0;
float Q_angle = 0;
float Q_gyro = 0;
float R_rate = 0;

PFont f; // Font

// Color scheme
color colorBg = #3F3F3F;
color colorFg = #DCDCCC;
color colorGyro = #CC9393;
color colorAcc = #7F9F7F;
color colorEst = #7F9F00;
color colorT1 = #7F007F;
color colorT2 = #7F007F;
color blue = #8CD0D3;

// Graph equations
class lineGyro implements ILine2DEquation{
  public double computePoint(double x,int pos) {
    return gyro;
  }		
}
class lineAcc implements ILine2DEquation{
  public double computePoint(double x,int pos) {
    return acc;
  }		
}
class lineEst implements ILine2DEquation{
  public double computePoint(double x,int pos) {
    return est;
  }		
}

RollingLine2DTrace rollingGyro,rollingAcc,rollingEst;
Graph2D g;

void setup () {
  // Environment
  size(1200, 800);
  //frameRate(100);

  // Serial
  println(Serial.list());
  myPort = new Serial(this, Serial.list()[0], 19200);
  myPort.bufferUntil('\n'); // don't generate a serialEvent() unless you get a newline character:

  // Font
  f = loadFont("DejaVuSansMono-16.vlw");

  // Rolling line traces
  rollingGyro = new RollingLine2DTrace(new lineGyro() ,10,0.01f);
  rollingGyro.setTraceColour(int(red(colorGyro)),int(green(colorGyro)),int(blue(colorGyro)));
	
  rollingAcc = new RollingLine2DTrace(new lineAcc(),10,0.01f);
  rollingAcc.setTraceColour(int(red(colorAcc)),int(green(colorAcc)),int(blue(colorAcc)));

  rollingEst = new RollingLine2DTrace(new lineEst(),10,0.01f);
  rollingEst.setTraceColour(int(red(colorEst)),int(green(colorEst)),int(blue(colorEst)));

  // Graph
  g = new Graph2D(this, width-150, height-100, false);
  g.addTrace(rollingGyro);
  g.addTrace(rollingAcc);
  g.addTrace(rollingEst);

  g.position.y = 50;
  g.position.x = 100;

  g.setYAxisMin(-90);
  g.setYAxisMax(90);
  g.setYAxisTickSpacing(10);
  g.setXAxisMax(10f);

  g.setNoBorder();
  g.setAxisColour(int(red(colorFg)),int(green(colorFg)),int(blue(colorFg)));
  g.setFontColour(int(red(colorFg)),int(green(colorFg)),int(blue(colorFg)));
}

void draw () {
  textFont(f,16);
  background(colorBg);
  g.draw();

  // Print data
  fill(colorGyro);
  textAlign(RIGHT);
  text(gyro,125,15);
  textAlign(LEFT);
  text("gyro",5,15);
  
  fill(colorAcc);
  textAlign(RIGHT);
  text(acc,125,30);
  textAlign(LEFT);
  text("acc",5,30);
  
  fill(colorEst);
  textAlign(RIGHT);
  text(est,125,45);
  textAlign(LEFT);
  text("est",5,45);

  fill(colorFg);
  textAlign(RIGHT);
  text(t1,270,15);
  textAlign(LEFT);
  text("t1",150,15);

  textAlign(RIGHT);
  text(t2,270,30);
  textAlign(LEFT);
  text("t2",150,30);

  // Print fps
  textFont(f,10);
  fill(colorFg);
  textAlign(RIGHT);
  text(frameRate,width-25,15);
  textAlign(LEFT);
  text("fps",width-25,15);
}


void serialEvent (Serial myPort) {
  String inString = myPort.readStringUntil('\n'); // get the ASCII string:
  
  if (inString != null) {
    // Clean the input
    String inList[] = split(inString, ',');
    gyro = float(inList[0]);
    acc = float(inList[1]);
    est = float(inList[2]);
   //t1 = float(inList[3]);
    //t2 = float(inList[4]);
  }
}

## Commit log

2012-01-15 Added Electronics
    [untitled.brd, untitled.sch]
2012-01-18 Arduino sofware, updated electronics and some report outline.
    [Mainboard.brd, Mainboard.sch]
2012-01-25 Split board
    [Motorcontroller.brd, Motorcontroller.sch]
2012-01-25 Added gyro calibration. Closes #6.
2012-02-08 Non-working kalman-filter
2012-02-10 Working non-tuned Kalman filter
2012-03-01 Mainboard 2.0. Fixes #1, #2 #12
    [Mainboard.brd, Mainboard.sch]
2012-03-06 Kalman trial and error
    [graph.pde, swagway.ino]
2012-03-07 Motorboard v2.0
    [Motorcontroller.brd, Motorcontroller.sch]
2012-03-08 Motorboard: pad sizes and small reroutes
    [Motorcontroller.brd]
2012-03-08 Few proximity reroutes
    [Motorcontroller.brd]
2012-03-09 Updated .sch to be consisting to .brd (it was missing from the last commit)
    [Motorcontroller.sch]
2012-03-09 Reroute around header
    [Motorcontroller.brd]
2012-03-09 Bumped version number and updated pdf
    [Motorcontroller.brd]
2012-03-15 Motor control scheme
2012-03-15 New motorboard test
2012-03-16 Trying to debug the gyro angle
2012-03-17 Test with PWM
2012-03-17 New Kalman-filter and some tidy-up
2012-03-21 Data cleaning and samples/sec
2012-03-26 Renamed HEXFETs so both bridge fit
    [Motorcontroller.brd, Motorcontroller.sch]
2012-03-26 Wrote the motor control scheme so it actually fits the electronics
2012-03-26 New mainboard. Closes #13, closes #21 and closes #9 as it becomes irrelevant.
    [Mainboard.brd, Mainboard.sch]
2012-03-26 Table with pin connections and updated motor control scheme
2012-03-29 Redesign of motorboard. Closes #30
    [Motorcontroller.brd, Motorcontroller.sch]
2012-03-29 Radio on mainboard. Closes #29
    [Mainboard.brd, Mainboard.sch]
2012-04-03 First test with gyro lib
2012-04-03 Reciving the right data from the gyro with the gyrolib. Closes #20
2012-04-03 More robust gyroSampleRate
2012-04-03 Framework for acc lib
2012-04-04 Parsed the news data from the gyro and acc to the Kalman-filter, better names and some clean-up.
2012-04-05 Brackets around serial package
2012-04-12 New motorcontroller with pull-down
    [Motorcontroller.brd, Motorcontroller.sch]
2012-04-13 Reroute and tidy-up. New version number
    [Motorcontroller.brd, Motorcontroller.sch]
2012-04-13 Updated motor control scheme to fit with the new motorboard
2012-04-13 Description of Motorcontroller versions
2012-04-17 Fixed airwire in motorboard. Updated .pdf and rapport
    [Motorcontroller.brd, Motorcontroller.sch]
2012-04-17 New Motorboard_test for the new motorcontroller
2012-04-20 First connection between IMU and motor
2012-04-24 Moved resistors to Motorboard. Closes #37
    [Mainboard.brd, Mainboard.sch, Motorcontroller.brd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]
2012-04-24 Updated .pdfs
    [Mainboard.brd, Motorcontroller.brd]
2012-04-24 Added LEDs to optocoupelers. Closes #39
    [Motorcontroller.brd, Motorcontroller.sch]
2012-04-24 Changed pins on pinheader
    [Motorcontroller.brd, Motorcontroller.sch]
2012-04-24 Route of small airwire
    [Motorcontroller.brd]
2012-04-24 Updated Motorcontroller and Mainboard changelog
2012-04-26 Test motorcontrol with static speed
2012-04-27 Proportional motorcontrol
2012-04-27 Changed pin 5 and 9. Closes #42
    [Mainboard.brd, Mainboard.sch]
2012-04-30 Added PID. Closes #3
2012-05-01 New type of PID
2012-05-03 Motorcontroller with protection diodes. Also closes #40
    [Motorcontroller.brd, Motorcontroller.sch]
2012-05-03 Updated .pdf
    [Motorcontroller.brd]
2012-05-07 Reset to motorcontroller v5.2
    [Motorcontroller.brd, Motorcontroller.sch]
2012-05-07 Added Motorcontroller v5.2 sch
2012-05-07 Added Motorcontroller v2.1 sch
2012-05-08 Changed I2C section
2012-05-08 PWM text and figure
2012-05-08 rewrote I2C section
2012-05-08 Edited small stuff in I2C, added gyro subsubsection
2012-05-09 Removed the PID tap. Closes #26 and closes #27
2012-05-10 Rewrote several parses of boards
2012-05-10 Rewrote motorboard section
2012-05-10 Gyro and acc theory and frontpage
2012-05-10 Rewrote motorboard issues
2012-05-10 society value of motion sensoring
2012-05-10 Added Accelerometer info
2012-05-10 Added basic I2C figure
    [I2Cbasic.sch]
2012-05-10 Added accbasic figure
    [accbasic.sch]
2012-05-10 Added subsections for steering part
2012-05-10 Added steering section
2012-05-10 Small changes to I2C
2012-05-11 Added I2C read and write
2012-05-11 clean-up and IMU biblioter init. atmega in bib
2012-05-11 Added text on filters
2012-05-11 IMU biblioteker
2012-05-11 More IMU bibliotek
2012-05-11 Last part of IMU lib
2012-05-11 Added H-brigde picture
    [hbrigde.sch]
2012-05-11 Moved boarddate to margin
2012-05-11 Picture of fried motorcontroller
2012-05-11 added pictures of old motorboards
2012-05-11 Added PID figure
